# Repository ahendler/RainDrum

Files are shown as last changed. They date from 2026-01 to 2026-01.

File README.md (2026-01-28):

## A 'Rain Drum' playing bot

Spun by a NEMA 17 stepper motor and hit by a mallet attached to a solenoid, controlled by an ESP32-C3 microcontroller via BLE MIDI.

<div style="display: flex; justify-content: center; gap: 20px; align-items: center;">
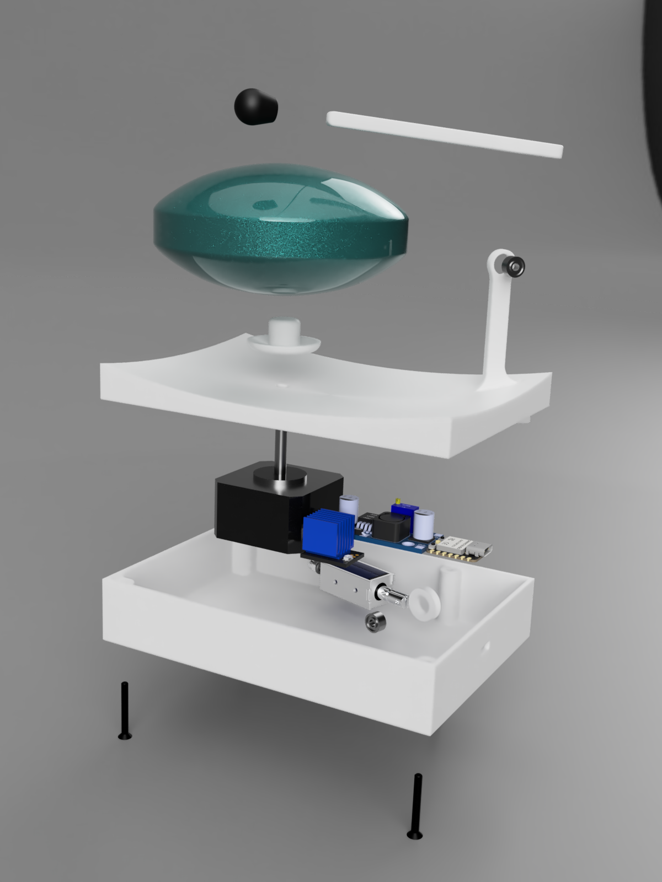
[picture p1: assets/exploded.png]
Exploded View
  
  Rain Drum Bot
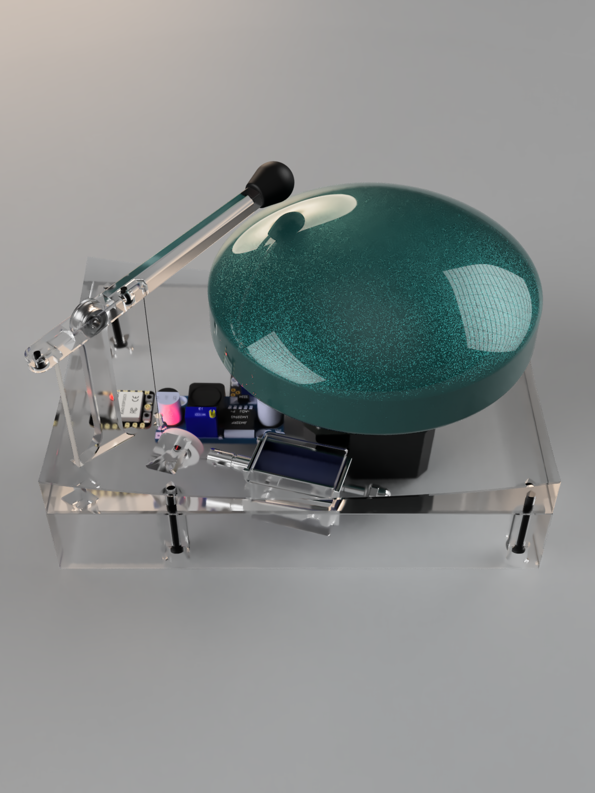
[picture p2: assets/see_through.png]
See Through
  
</div>

## Repo structure
- `src/RainDrum/` - Main firmware code for the ESP32-C3 microcontroller
- `parts/` - 3D models and Bill of Materials
- `assets/` - Images and videos of the project
- `src/tuning_scripts/` - Utilities to find experimental acceleration and speed values

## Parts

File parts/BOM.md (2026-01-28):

# Bill of Materials

## Eletronic Components
- Stepper Motor Driver TMC2209
- Voltage Step Down Module 12V to 5V
- 12V Solenoid TAU-0530
- DC Power Supply 12V 2A
- NEMA 17 Stepper Motor 42x23mm
- ESP32 C3 Super Mini
- Barrel Jack Connector

## Mechanical Components
- M3x25mm Screws (6x)
- M3x8mm Screws (6x)
- 693zz Bearings (2x)

## Misc
- Mini Steel tongue drum "Rain Drum" with drumstick ([AliExpress](https://a.aliexpress.com/_mKWVIeN))
- Nylon string
- Rubber Feet
- Mini hair rubber bands (for solenoid return)

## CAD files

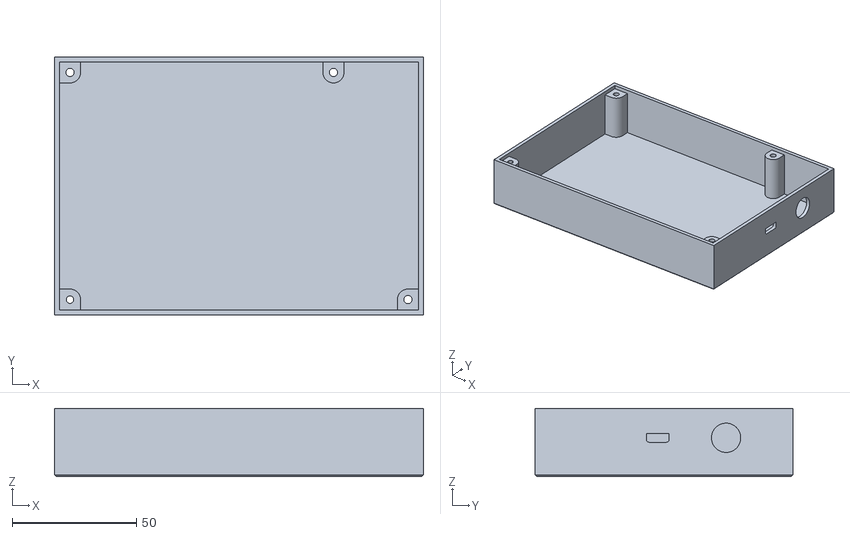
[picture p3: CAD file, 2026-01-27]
parts/STL/bottom_housing.stl
148.6 x 104.0 x 27.4

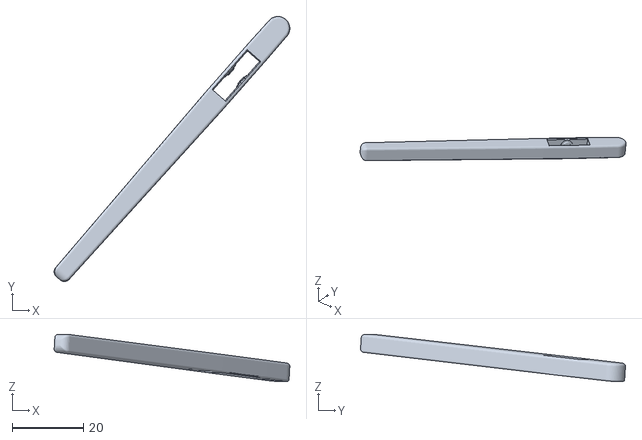
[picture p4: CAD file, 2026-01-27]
parts/STL/mallet.stl
66.3 x 74.6 x 13.3

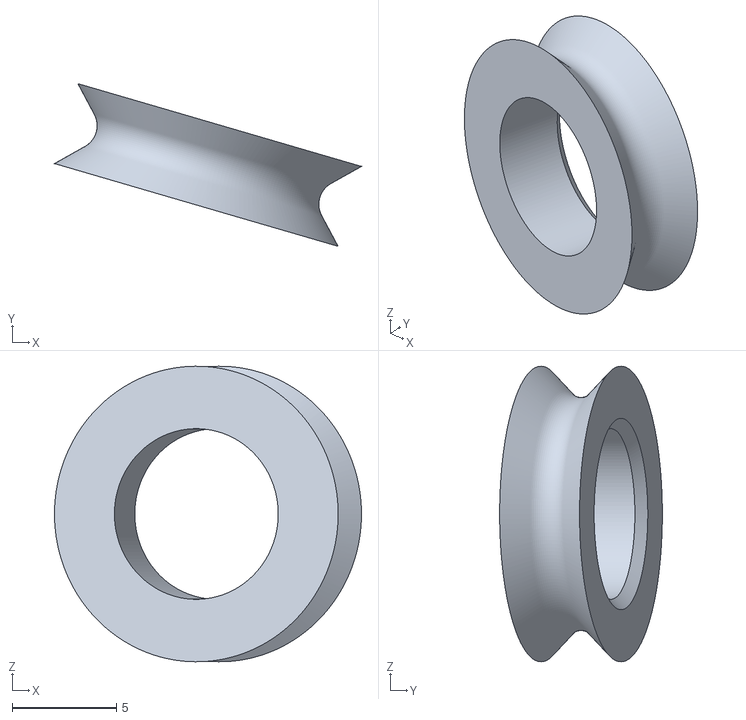
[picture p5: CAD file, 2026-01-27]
parts/STL/pulley.stl
14.8 x 7.82 x 14.2

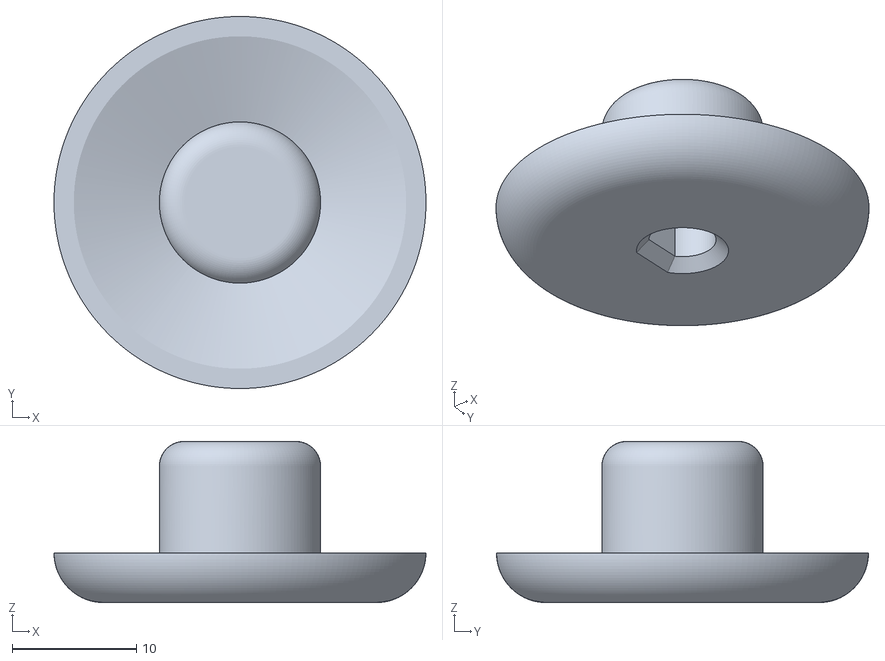
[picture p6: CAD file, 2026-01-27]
parts/STL/motor_shaft_to_drum.stl
30.0 x 30.0 x 13.0

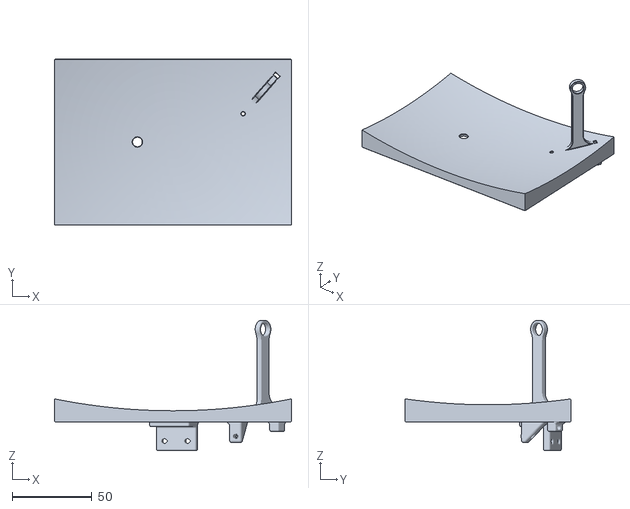
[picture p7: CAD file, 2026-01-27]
parts/STL/base.stl
148.6 x 104.0 x 81.7

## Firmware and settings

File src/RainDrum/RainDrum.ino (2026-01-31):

#include "Drum.h"
#include "MidiBle.h"
#define ARDUINO_USB_CDC_ON_BOOT 1
#define ARDUINO_USB_MODE 1

// MidiBle is only supported on espressif/arduino-esp32 core version 2.0.17 and below

MidiBle midiListener;
Drum drumPlayer;

void setup() {
    Serial.begin(115200);
    drumPlayer.initialize();
    midiListener.initialize();
    Serial.println("Rain Drum Initialized");
}

void loop() {
    midiListener.read();
    if (midiListener.noteToPlay != -1) {
        drumPlayer.moveToPositionAndStrike(midiListener.noteToPlay);
        midiListener.noteToPlay = -1;
    }
}

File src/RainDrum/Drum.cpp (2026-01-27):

#include "Drum.h"

// Hardware pins
#define STEP_PIN 9
#define DIR_PIN 8
#define EN_PIN 7
#define STICK_A 20
#define STICK_B 21

Drum::Drum() : stepper(AccelStepper::DRIVER, STEP_PIN, DIR_PIN) {}

void Drum::initialize() {
    pinMode(EN_PIN, OUTPUT);
    digitalWrite(EN_PIN, HIGH); // Disable motor initially
    pinMode(STICK_A, OUTPUT);
    digitalWrite(STICK_A, HIGH);
    pinMode(STICK_B, OUTPUT);
    digitalWrite(STICK_B, HIGH);
    // Configure stepper
    float maxSpeedSteps = (STEPS_PER_REV * MAX_RPM) / 60.0;
    stepper.setMaxSpeed(maxSpeedSteps);
    stepper.setAcceleration(MAX_ACCELERATION);
    // Enable motor
    digitalWrite(EN_PIN, LOW); //need to disable it later (positioning may drift)
    // Calculate minMoveTime based on max acceleration
    // We always start from rest and accelreate for half the distance, then decelerate
    // t = sqrt(2(s/2)/a) * 2 = 2*sqrt(s/a)
    // We also always want the movement to take the same time regardless of distance
    // So our minMoveTime is based on the max distance (4 notes = 800 steps)
    minMoveTime = 2.0 * sqrt( 800 / MAX_ACCELERATION );
    // for a MAX_ACCELERATION of 45000, minMoveTime = 0.266s
}

void Drum::moveToPosition(int targetDrumPosition) {
    // Move the drum to the specified position in a blocking manner
    int posToMove = (targetDrumPosition - currentDrumPosition + 8) % 8;
    if (posToMove > 4) posToMove -= 8; // Choose shortest path
    int stepsToMove = posToMove * STEPS_PER_NOTE;

    // Base case, no movement needed
    if (stepsToMove == 0) {
        delay(minMoveTime * 1000); // Delay minMoveTime to keep timing consistent
        return;
    }

    // Max speed isn't relevant since we are acceleration-limited
    // Set it to a high value to avoid limiting the motion
    stepper.setMaxSpeed(MAX_RPM * STEPS_PER_REV / 60.0);

    // Calculate required acceleration to complete move in minMoveTime
    // a = 4s/t^2
    float requiredAcceleration = (4.0 * abs(stepsToMove)) / (minMoveTime * minMoveTime);

    stepper.setAcceleration(requiredAcceleration);
    long targetSteps = stepper.currentPosition() + stepsToMove;
    stepper.moveTo(targetSteps);

    while (stepper.distanceToGo() != 0) {
        stepper.run();
    }

    currentDrumPosition = targetDrumPosition; 
}

void Drum::strike() {
    digitalWrite(STICK_A, LOW);
    delay(20); // Strike duration
    digitalWrite(STICK_A, HIGH);
}

void Drum::moveToPositionAndStrike(int position) {
    moveToPosition(position);
    strike();
    Serial.println("Struck position " + String(position));
}

const int Drum::STEPS_PER_REV = 1600;
const int Drum::STEPS_PER_NOTE = 200;
const float Drum::MAX_RPM = 3000.0f; // irrelevant (acceleration-limited)
const float Drum::MAX_ACCELERATION = 45000.0f; // steps/sec^2 - Measured to be between 40,000 and 48,000

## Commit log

2026-01-27 Improve Stepper Kinematics
2026-01-27 Add STLs
    [base.stl, bottom_housing.stl, mallet.stl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]
2026-01-28 Add BOM
2026-01-28 Update photo and BOM
